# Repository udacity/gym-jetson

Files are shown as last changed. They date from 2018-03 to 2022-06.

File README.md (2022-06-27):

# Archival Note
We are archiving this repository because we do not want learners to push personal development to the current repository. If you have any issues or suggestions to make, feel free to:
- Utilize the https://knowledge.udacity.com/ forum to seek help on content-specific issues.
- Submit a support ticket along with the link to your forked repository if (learners are) blocked for other reasons. Here are the links for the [retail consumers](https://udacity.zendesk.com/hc/en-us/requests/new) and [enterprise learners](https://udacityenterprise.zendesk.com/hc/en-us/requests/new?ticket_form_id=360000279131). 

Udacity - Robotics NanoDegree Program (https://www.udacity.com/robotics)
# Learning Robotics on the Jetson TX2 - Lights Out Robot

Are you ready to learn how to use your Jetson TX2 for robotics applications? In this project, you'll learn how to get started using your TX2 to apply AI to your robotics application. You will get the chance to build a simple “Lights Out” robot that will use reinforcement learning to push buttons and turn out corresponding LEDs. We will cover how to wire up, program, and run the robot. Additionally, we will discuss the basics of applied reinforcement learning.



## Getting Started

1. Start by ordering the parts and gathering the tools listed in the [Bill of Materials](https://github.com/udacity/gym-jetson/blob/master/robot_construction/BOM.md) More information about laser cutting, such as size and thickness of material can also be found there. You will also find the .eps or .dxf file used to laser cut this robot. If you don't have access to a laser cutter, information about ordering the parts using a laser cutting production service is included.

2. Set up your Jetson environment. This project was run on jetPack3.2, and was also tested on 3.1. Python libraries gpio, cffi, smbus, and numpy are required.

```
sudo apt-get install libffi-dev
sudo pip install cffi
sudo pip install smbus-cffi numpy gpio
```

3. Follow the steps for [Assembling the Robot](https://github.com/udacity/gym-jetson/blob/master/robot_construction/assembly.md) 

4. Jupyter notebooks have been created for this project to outline the next steps. The first notebook covers **taking control of the robot**, including assembly and wiring of the electronic components, testing and troubleshooting getting the arm to hit the buttons and have the lights turn on and off. A second notebook discusses **the reinforcement learning component, where we program the robot to play a game**.

To launch the [notebook](https://github.com/udacity/gym-jetson/blob/master/0_Introduction.ipynb) locally from your machine, run the following commands:

``` bash
$ git clone https://github.com/udacity/gym-jetson.git
$ cd gym-jetson
$ jupyter notebook 0_Introduction.ipynb
```

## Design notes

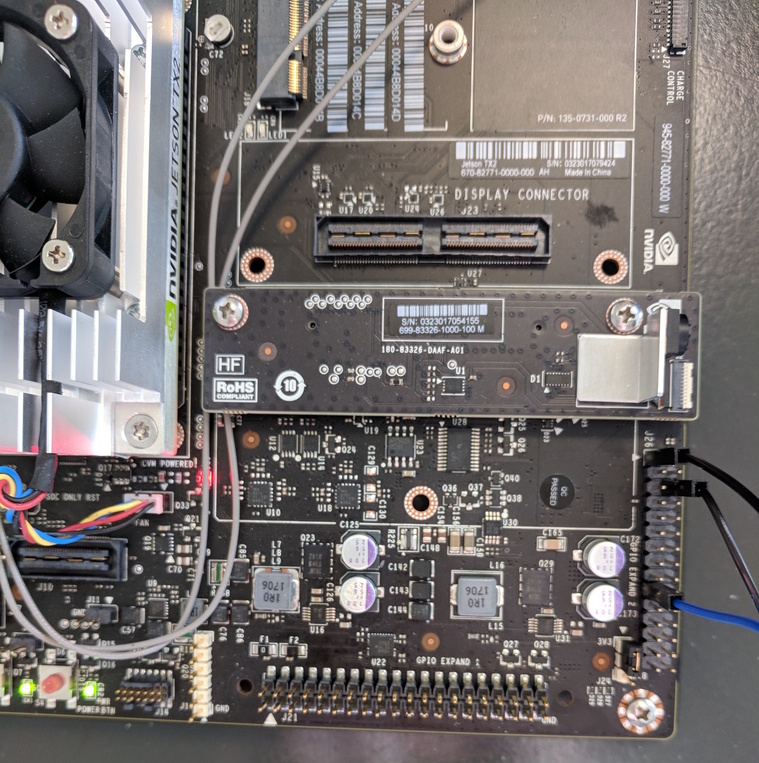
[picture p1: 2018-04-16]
images/jetson4.jpg

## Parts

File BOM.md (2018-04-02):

## Bill of Materials

### Lights Out Robot

| Vendor | Part | Qty.  |
| --- | --- | ----- |
| Sparkfun | [Servo - Hitec HS-422 (Standard Size)](https://www.sparkfun.com/products/11884) | 2 |
| Sparkfun | [Tactile Button Assortment](https://www.sparkfun.com/products/10302) | 1 |
| Sparkfun | [Diffused LED - Blue 10mm](https://www.sparkfun.com/products/10635) | 1 |
| Sparkfun | [Diffused LED - Green 10mm](https://www.sparkfun.com/products/10633) | 1 |
| Sparkfun | [Diffused LED - Yellow 10mm](https://www.sparkfun.com/products/10634) | 1 |
| Sparkfun | [Diffused LED - Red 10mm](https://www.sparkfun.com/products/10632) | 1 |
| Sparkfun | [LED Holder - 10mm (Chrome Finish)](https://www.sparkfun.com/products/11148) | 4 |
| Sparkfun | [SparkFun Pi Servo HAT](https://www.sparkfun.com/products/14328) | 1 |
| Sparkfun | [Resistor 1K Ohm 1/4th Watt PTH - 20 pack](https://www.sparkfun.com/products/13760) | 1 |
| Sparkfun | [Resistor 100 Ohm 1/4th Watt PTH - 20 pack](https://www.sparkfun.com/products/13761) | 1 |
| Sparkfun | [Transistor - NPN (BC337)](https://www.sparkfun.com/products/13689) | 4 |
| Sparkfun | [Machine Screw - Socket Head (6-32 ; 3/8"; 25 pack)](https://www.sparkfun.com/products/12423) | 1 |
| Sparkfun | [Standoff - Aluminum Threaded (6-32; 1-1/4", 4 Pack)](https://www.sparkfun.com/products/13136) | 1 |
| Sparkfun | [Breadboard - Full-Size (Bare)](https://www.sparkfun.com/products/12615) | 1 |
| Sparkfun | [Nut - Metal (4-40, 10 pack)](https://www.sparkfun.com/products/10454) | 1 |
| Sparkfun | [Screw - Phillips Head (1/2", 4-40, 10 pack)](https://www.sparkfun.com/products/10452) | 1 |
| Sparkfun | [Jumper Wires - Connected 6" (M/F, 20 pack)](https://www.sparkfun.com/products/12794) | 1 |
| Sparkfun | [Jumper Wire Kit](https://www.sparkfun.com/products/124) | 1 |
| Sparkfun | [Silicone Bumpers - Large (10x16.5mm, 4 pack)](https://www.sparkfun.com/products/10594) | 1 |
| Fastenal | [Screws for servo horns](https://www.fastenal.com/products/details/75403) | 4 |
| Amazon | [HELLOYEE 2x20 Pins Extra Tall Female 0.1" Pitch Stacking Header for Raspberry Pi A+ Pi Model B+ Pi 2 Pi 3 (Pack of 5)](https://www.amazon.ca/HELLOYEE-Female-Stacking-Header-Raspberry/dp/B071VFG82G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) | 1 |

Laser cut [base and arm](https://github.com/udacity/gym-jetson/blob/master/gtc_base_arm.dxf) on 3mm acrylic

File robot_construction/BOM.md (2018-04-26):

## Bill of Materials

### Lights Out Robot

Laser cut [base and arm dxf](https://github.com/udacity/gym-jetson/blob/master/robot_construction/gtc_base_arm.dxf) or [base and arm eps](https://github.com/udacity/gym-jetson/blob/master/robot_construction/gtc_base_arm.eps)on 3mm acrylic. This design is just under 1 square foot of material (approimately 30.5 cm squared). 

If you do not have access to a laser cutter, you can use a service such as [Ponoko](https://www.ponoko.com/) to have the file cut and sent to you! To do this, you can add a new design > upload your design > navigate to gtc_base_arm.dxf or gtc_base_arm.eps > add material (select plastic) > choose a material (select acrylic, your choice of colour) > choose a thickness (3.0mm) > choose a size (P2 - 384mm). Select "add this material" and "Make it"! 

| Vendor | Part | Qty.  |
| --- | --- | ----- |
| Adafruit | [Standard servo - TowerPro SG-5010 - 5010](https://www.adafruit.com/product/155) | 2 |
| Sparkfun | [Tactile Button Assortment](https://www.sparkfun.com/products/10302) | 1 |
| Sparkfun | [Diffused LED - Blue 10mm](https://www.sparkfun.com/products/10635) | 1 |
| Sparkfun | [Diffused LED - Green 10mm](https://www.sparkfun.com/products/10633) | 1 |
| Sparkfun | [Diffused LED - Yellow 10mm](https://www.sparkfun.com/products/10634) | 1 |
| Sparkfun | [Diffused LED - Red 10mm](https://www.sparkfun.com/products/10632) | 1 |
| Sparkfun | [LED Holder - 10mm (Chrome Finish)](https://www.sparkfun.com/products/11148) | 4 |
| Sparkfun | [SparkFun Pi Servo HAT](https://www.sparkfun.com/products/14328) | 1 |
| Sparkfun | [Resistor 1K Ohm 1/4th Watt PTH - 20 pack](https://www.sparkfun.com/products/13760) | 1 |
| Sparkfun | [Resistor 100 Ohm 1/4th Watt PTH - 20 pack](https://www.sparkfun.com/products/13761) | 1 |
| Sparkfun | [Transistor - NPN (BC337)](https://www.sparkfun.com/products/13689) | 4 |
| Sparkfun | [Machine Screw - Socket Head (6-32 ; 3/8"; 25 pack)](https://www.sparkfun.com/products/12423) | 1 |
| Sparkfun | [Standoff - Aluminum Threaded (6-32; 1-1/4", 4 Pack)](https://www.sparkfun.com/products/13136) | 1 |
| Sparkfun | [Breadboard - Full-Size (Bare)](https://www.sparkfun.com/products/12615) | 1 |
| Sparkfun | [Nut - Metal (4-40, 10 pack)](https://www.sparkfun.com/products/10454) | 1 |
| Sparkfun | [Screw - Phillips Head (1/2", 4-40, 10 pack)](https://www.sparkfun.com/products/10452) | 1 |
| Sparkfun | [Jumper Wires - Connected 6" (M/F, 20 pack)](https://www.sparkfun.com/products/12794) | 1 |
| Sparkfun | [Jumper Wire Kit](https://www.sparkfun.com/products/124) | 1 |
| Sparkfun | [Silicone Bumpers - Large (10x16.5mm, 4 pack)](https://www.sparkfun.com/products/10594) | 1 |
| Fastenal | [Screws for servo horns](https://www.fastenal.com/products/details/75403) | 4 |
| Amazon | [HELLOYEE 2x20 Pins Extra Tall Female 0.1" Pitch Stacking Header for Raspberry Pi A+ Pi Model B+ Pi 2 Pi 3 (Pack of 5)](https://www.amazon.ca/HELLOYEE-Female-Stacking-Header-Raspberry/dp/B071VFG82G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) | 1 |

### Tools Required
| Tool | Notes |
| --- |--- |
| Soldering Iron |  |
| Solder | |
| Wire cutter/ stripper | |
| Glue Gun + Glue | If your robot parts have been cut from acrylic, you could also use acrylic solvent to attach the pieces |
| Flat head screwdriver | |
| Phillips head screwdriver | |
| Socket head driver or allen key | |

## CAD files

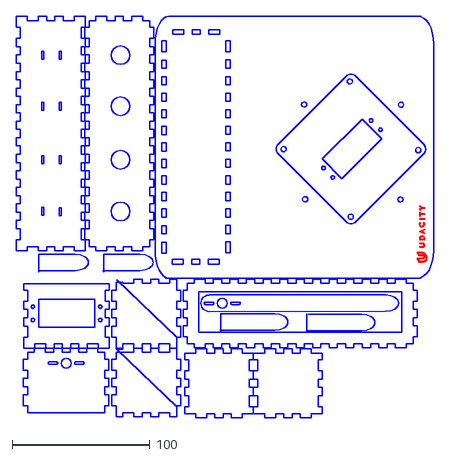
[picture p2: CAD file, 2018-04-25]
robot_construction/gtc_base_arm.dxf
302.8 x 291.3

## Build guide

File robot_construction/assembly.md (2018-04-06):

## Assembly Steps

Before we can use the servo HAT, we need to solder the extra tall 40 pin stacking header onto the servo HAT. Look at the image below to understand how to do this so that it can be plugged into the Jetson and still allow us to plug wires into the exposed pins later on.

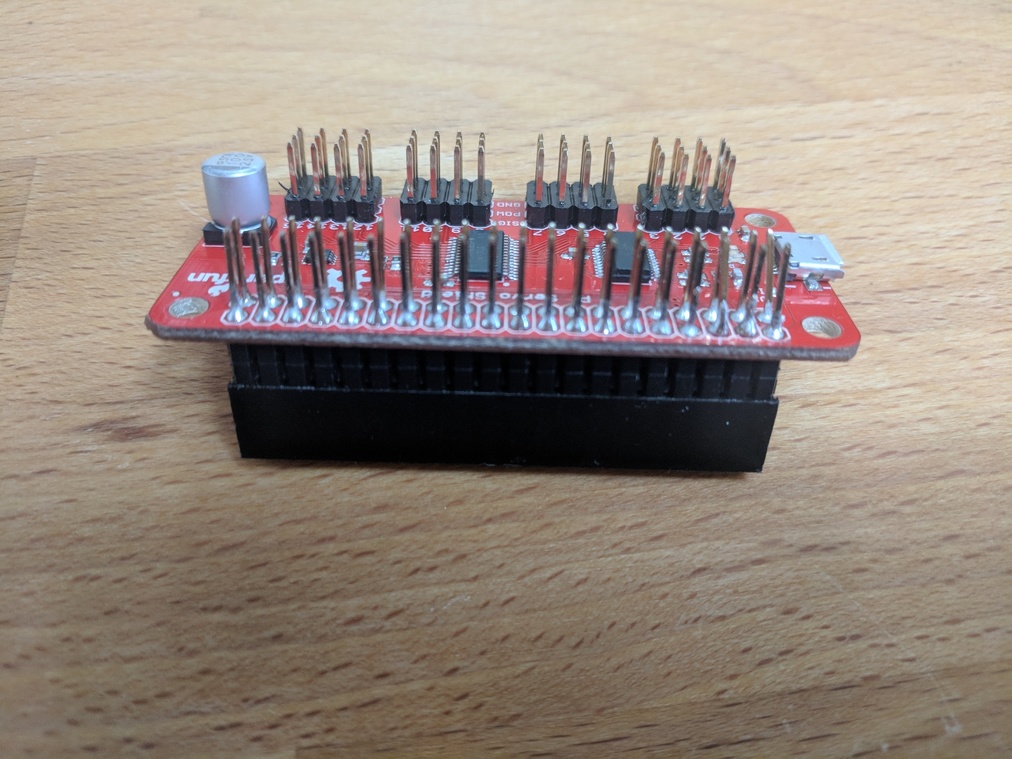
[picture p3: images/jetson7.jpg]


Next,lets use the Jetson and the servo HAT to "zero" both servos to a PWM start time of 0 and an end time of 1250. This will put the servos into a neutral position before we attach the base and arm. This will ensure that the arm is in a starting position from which the positions of the buttons have been calculated to correspond to in later steps.

To do this, plug the servo HAT into the Jetson J21 header as shown below, and plug the pan servo into channel 0 and the tilt servo into channel 1.

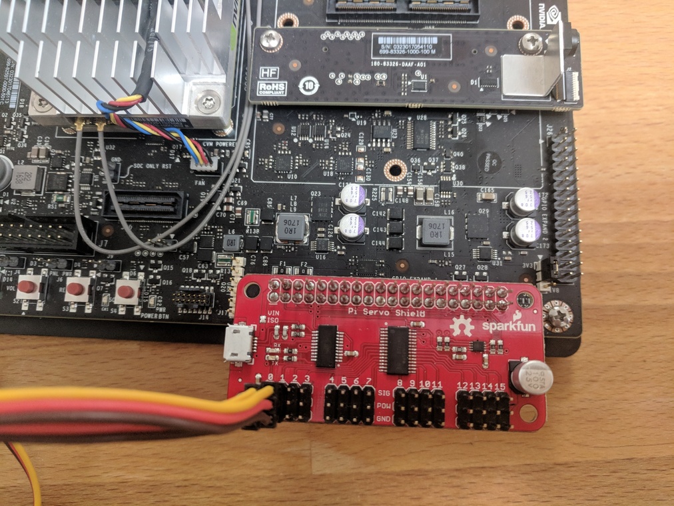
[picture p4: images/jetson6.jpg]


Put the code below into a .py file on the Jetson, and run to initialise the i2c device and write 0 and 1250 as start and stop times to both channel 0 and channel 1 of the HAT. You can find more information about i2c, smbus, and the specific channels that we are writing data to in later steps in the Jupyter notebook.

```
import smbus

#create object of type SMBus, attach it to bus "1"of the Jetson
bus = smbus.SMBus(1)

#the default address of the PWM servo hat is 0x40
addr = 0x40

#enable the PWM chip and tell it to automatically increment addresses after a write to allow for single operation multi-byte writes
bus.write_byte_data(addr, 0, 0x20)
bus.write_byte_data(addr, 0xfe, 0x1e)

#write a start time 0 to the PWM chip for channel 0 and channel 1
bus.write_word_data(addr, 0x06, 0)
bus.write_word_data(addr, 0x0A, 0)

#write an end time to channel 0 and channel 1, which will set the servo motors to their starting position
bus.write_word_data(addr, 0x0C, 1250)
bus.write_word_data(addr, 0x08, 1250)

bus.close()
```

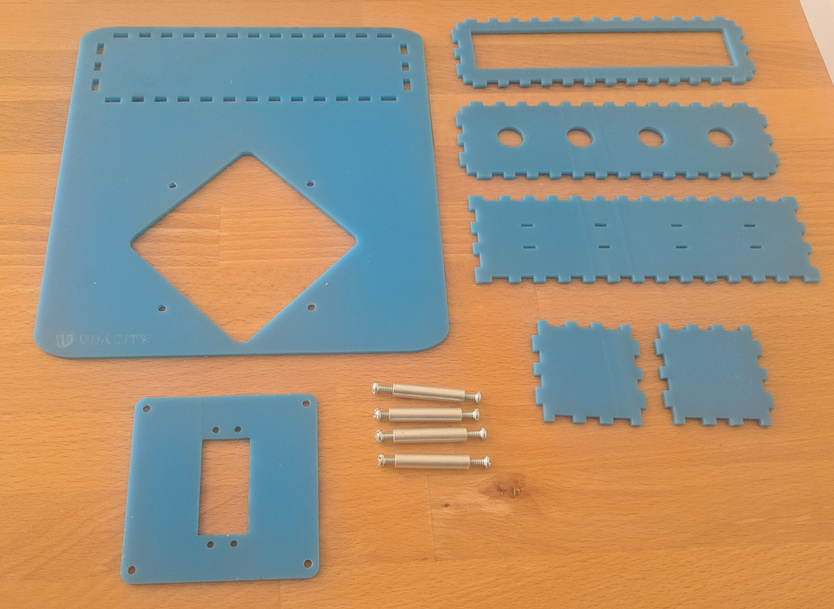
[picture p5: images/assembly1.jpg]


Now we will move on to the assembly of the base!

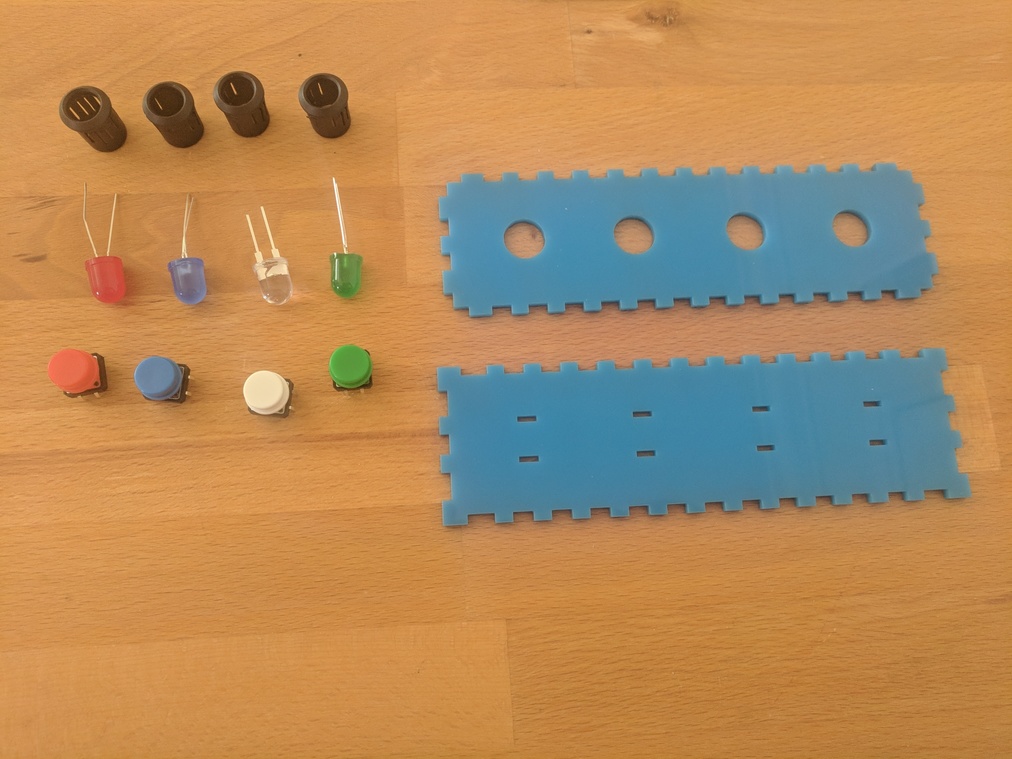
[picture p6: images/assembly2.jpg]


Push an LED into each holder, and attach one to each circular hole on acrylic LED panel assembly.
Set a button in each of the cutouts on the acrylic button panel. Two button leads will sit in each of the rectancular cutouts.
The base of the button will sit flush with the surface of the acrylic button panel. Add a dab of hot glue under each button to attach it to the surface.

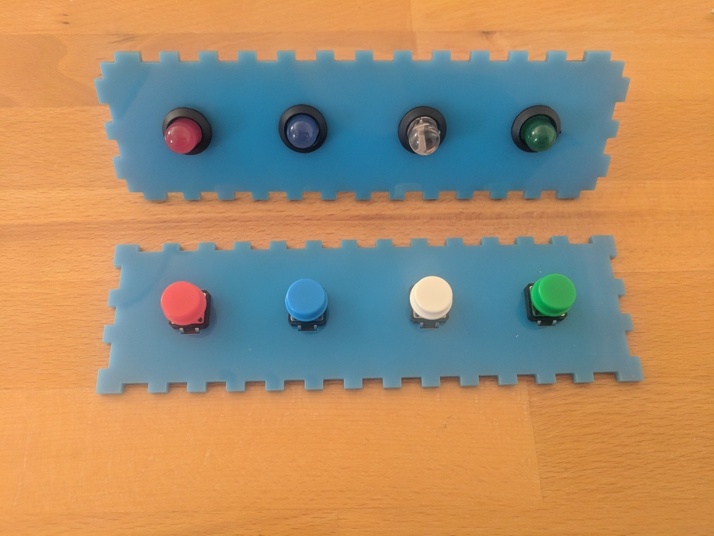
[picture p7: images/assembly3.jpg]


Solder a wire to each LED lead, and add shrink tubing to cover the connection. 
Solder a wire to two of the button leads as shown in the image below.

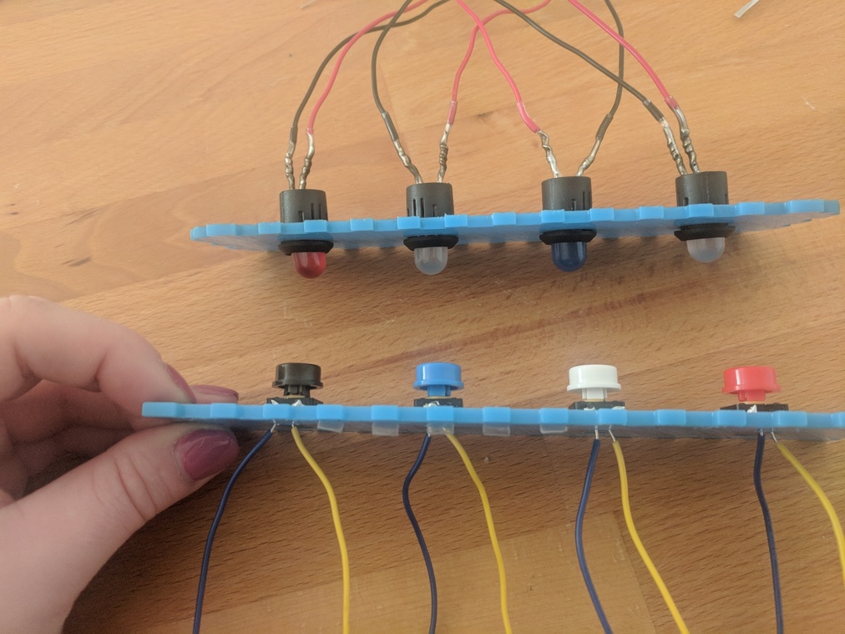
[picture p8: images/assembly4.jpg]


Assemble the button/led panel box, using the side and back pieces. Feed the wires through the rectangular cutout on the back panel. Add some hot glue to the interior edges of the box to adhere.

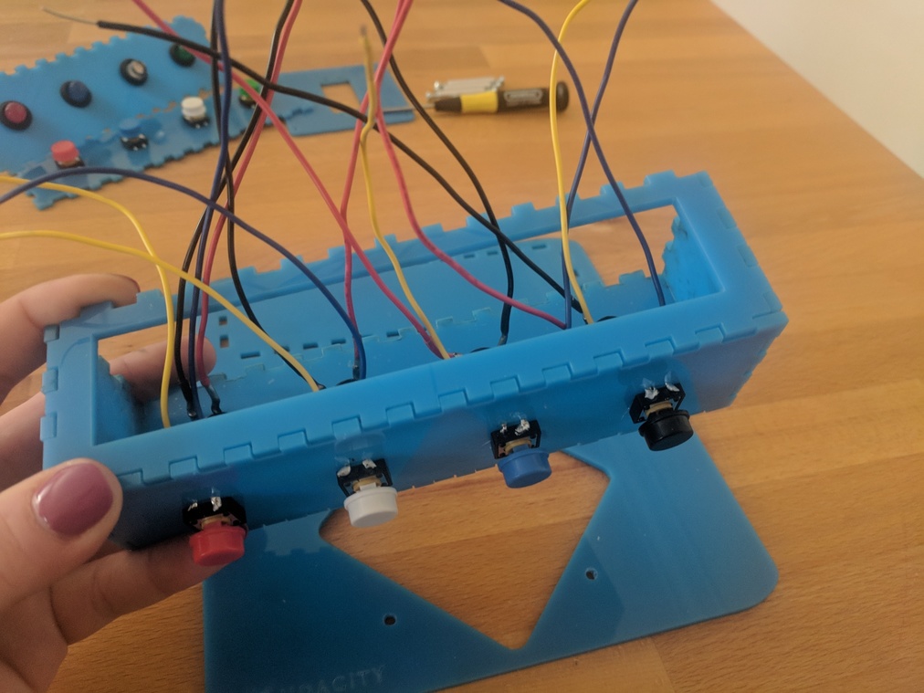
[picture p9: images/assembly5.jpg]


Insert the button/LED panel box into the slots of the robot base plate. Add some hot glue to adhere.

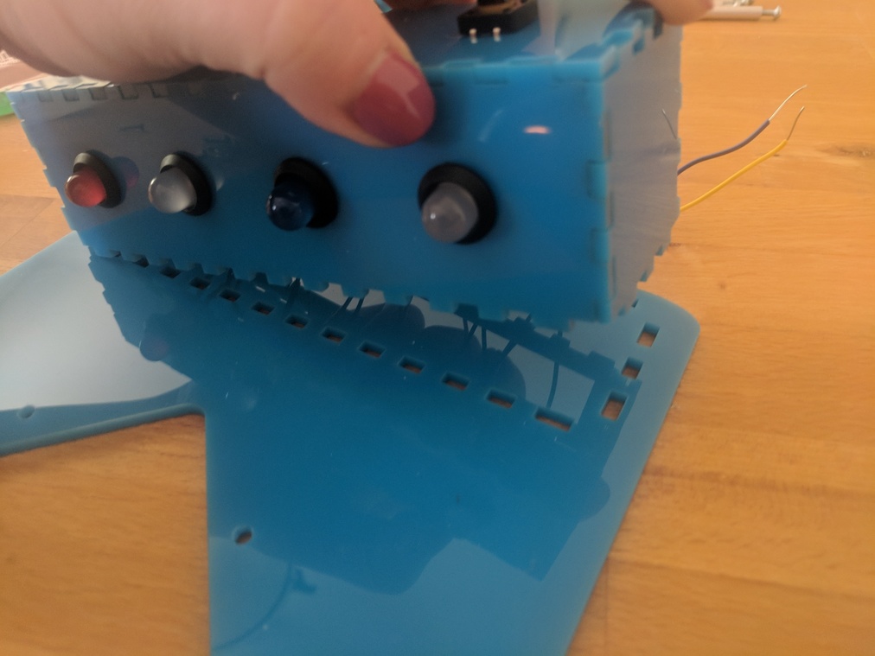
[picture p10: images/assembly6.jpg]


Attach one of the servos to the pan servo base plate as shown in the image below, using 4 screws and 4 nuts.

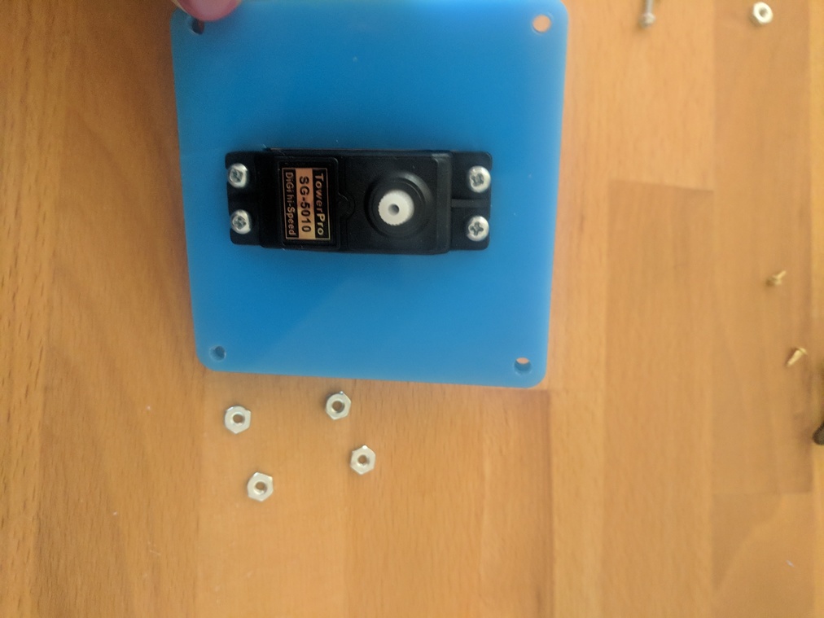
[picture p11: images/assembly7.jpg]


Attach the pan servo base plate to the robot base plate using 4 aluminum standoffs and 8 6-32 screws.

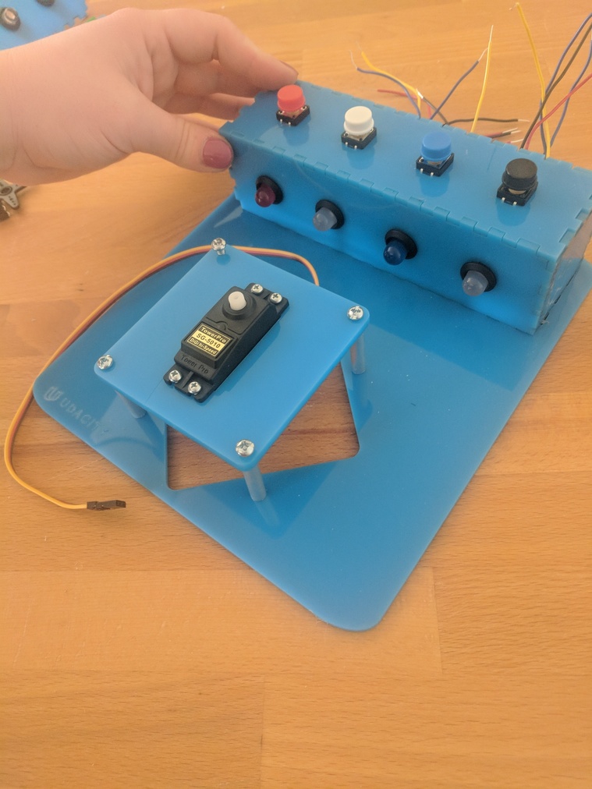
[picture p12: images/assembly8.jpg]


Attach the other servo to the vertical servo plate as shown below using 4 screws and 4 nuts. Also, attach the circular servo horn to the tilt servo base using 2 small gold screws.

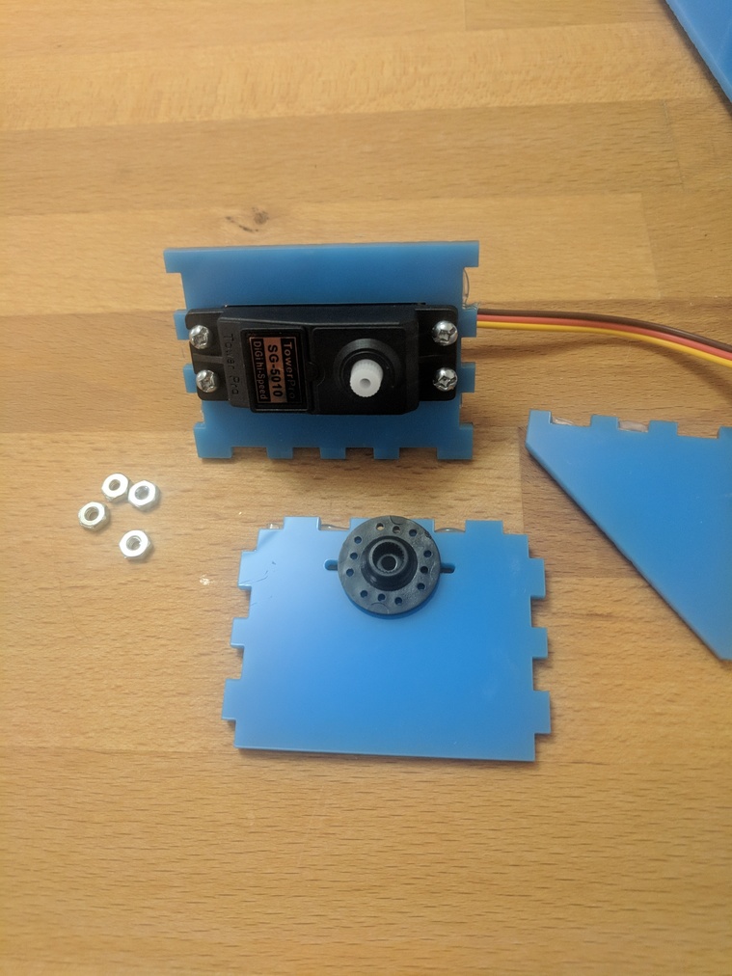
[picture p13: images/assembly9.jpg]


BEFORE the next step, make sure you have used the Jetson and the servo HAT to "zero" the pan servo to a PWM start time of 0 and an end time of 1250 as shown in the first step of this assembly document.

Using the small screw from the servo kit, screw the servo horn/ tilt sevo base to the pan servo as shown below. The orientation of this piece is very important!

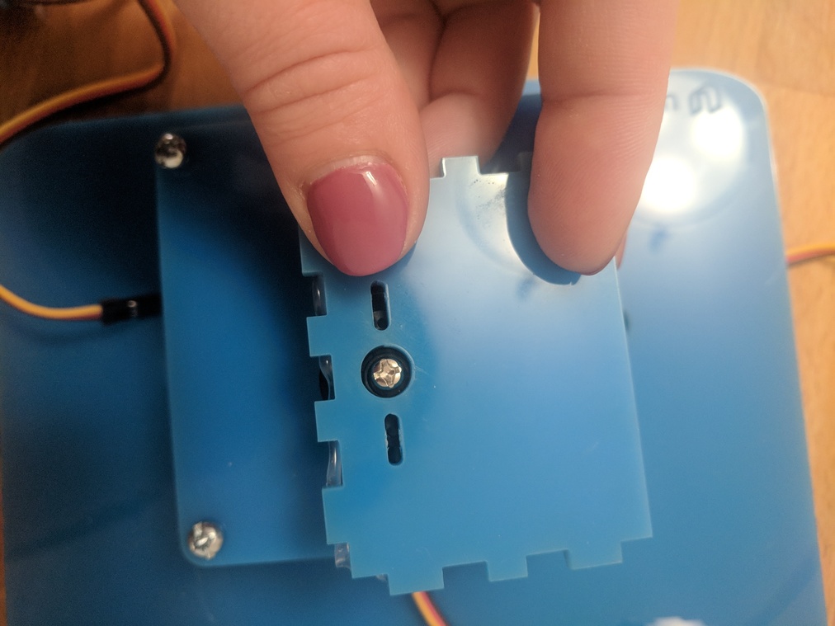
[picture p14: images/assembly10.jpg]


Affix the vertical servo plate and the two triangular support pieces to the tilt servo base in the orientation shown in the image below.

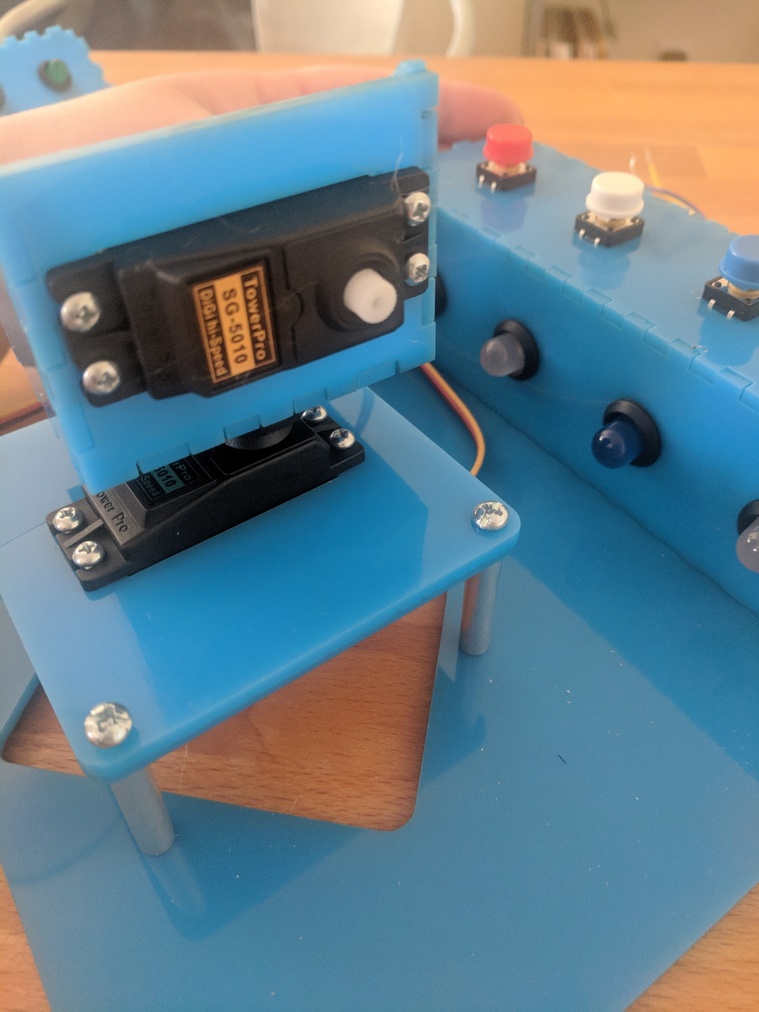
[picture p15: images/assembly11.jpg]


BEFORE the next step, make sure you have used the Jetson and the servo HAT to "zero" the tilt servo to a PWM start time of 0 and an end time of 1250.

Attach the 4-prong servo horn to the robot arm using 2 small gold screws. Using the small screw from the servo kit, screw the servo horn/ robot arm to the tilt servo as shown below. The angle and orientation of this piece is very important.

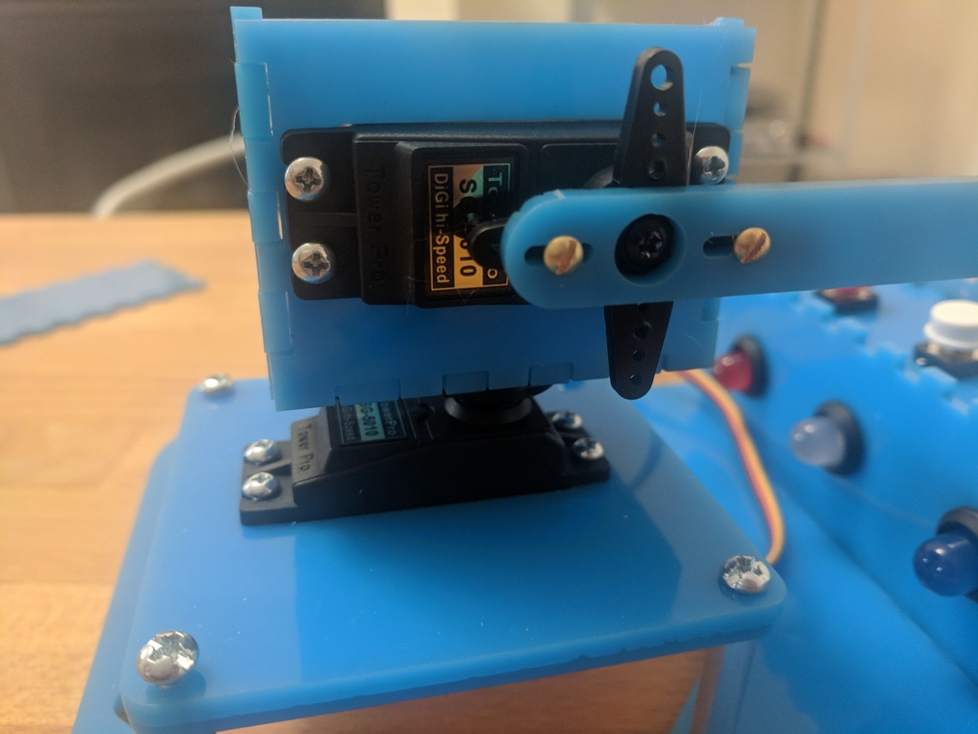
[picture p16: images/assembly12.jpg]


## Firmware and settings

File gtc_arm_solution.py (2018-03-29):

import random
import smbus
import time
import gpio
import sys
import numpy as np
import math
from collections import defaultdict
from jetson_env import JetsonEnv

#assign Jetson sysfs GPIO pins 
in_zero = 300
out_zero = 388

in_one = 398
out_one = 298

in_two = 389
out_two = 299

in_three = 481
out_three = 488

#TODO: change the PWM endtime values below to change the positions the servos move to
#increase the position values to move the arm to the left, and decrease to move to the right. 1 degree = 4.6
position_zero = 1594
position_one = 1457
position_two = 1275
position_three = 1091

arm_neutral = 1250 
#TODO: decrease arm_pressed to move the arm closer to the buttons/ press harder
arm_pressed = 900

#set up the GPIO pins as inputs or outputs, and set outputs to 0
gpio.setup(in_zero, gpio.IN)     # button 0
gpio.setup(out_zero, gpio.OUT)   # led 0
gpio.output(out_zero, 0) #set led 0 to low/off

gpio.setup(in_one, gpio.IN)     # button 1
gpio.setup(out_one, gpio.OUT)   # led 1
gpio.output(out_one, 0) #set led 1 to low/off

gpio.setup(in_two, gpio.IN)    # button 2
gpio.setup(out_two, gpio.OUT)  # led 2
gpio.output(out_two, 0) #set led 2 to low/off

gpio.setup(in_three, gpio.IN)    # button 3
gpio.setup(out_three, gpio.OUT)  # led 3
gpio.output(out_three, 0) #set led 3 to low/off

#create object of type SMBus, attach it to bus "1"of the Jetson
bus = smbus.SMBus(1)

#the default address of the PWM servo hat is 0x40
addr = 0x40
#enable the PWM chip and tell it to automatically increment addresses after a write to allow for single operation multi-byte writes
bus.write_byte_data(addr, 0, 0x20)
bus.write_byte_data(addr, 0xfe, 0x1e)
#write a start time 0 to the PWM chip for channel 0 and channel 1
bus.write_word_data(addr, 0x06, 0)
bus.write_word_data(addr, 0x0A, 0)
#write an end time to channel 0 and channel 1, which will set the servo motors to their starting position
bus.write_word_data(addr, 0x0C, arm_neutral)
bus.write_word_data(addr, 0x08, position_zero)


def led_status():
    """checks each led status, returns which LED currently high"""
    if gpio.read(out_zero) == 1:
        return 0    
    elif gpio.read(out_one) == 1:
        return 1
    elif gpio.read(out_two) == 1:
        return 2
    elif gpio.read(out_three) == 1:
        return 3
    else:
        return 4 # all LEDs are low

def move_to_position(m):
    """change the position of the arm base by writing new end time to PWM chip for channel 0 of servo hat"""
    if m == 0:
        time.sleep(.5)
        bus.write_word_data(addr, 0x08, position_zero)
    elif m == 1:
        time.sleep(.5)
        bus.write_word_data(addr, 0x08, position_one)
    elif m == 2:
        time.sleep(.5)
        bus.write_word_data(addr, 0x08, position_two)
    elif m == 3:
        time.sleep(.5)
        bus.write_word_data(addr, 0x08, position_three)


def push_button(led):
    """change the angle of the arm by writing new end time to PWM chip for channel 1 of servo hat"""
    time.sleep(.5)
    bus.write_word_data(addr, 0x0C, arm_pressed)
    time.sleep(.5)
    bus.write_word_data(addr, 0x0C, arm_neutral)
    button_led_check(led)


def button_led_check(led):
    """checks status of all buttons, and if the correct button has been pressed, LED turns off"""
    button_zero = gpio.read(in_zero)
    button_one = gpio.read(in_one)
    button_two = gpio.read(in_two)
    button_three = gpio.read(in_three)

    if led == 0 and button_zero == 1:
        gpio.output(out_zero, 0)
    elif led == 1 and button_one == 1:
        gpio.output(out_one, 0)
    elif led == 2 and button_two == 1:
        gpio.output(out_two, 0)
    elif led == 3 and button_three == 1:
        gpio.output(out_three, 0)


def dance():
    bus.write_word_data(addr, 0x08, 1594)
    bus.write_word_data(addr, 0x08, 1091)
    bus.write_word_data(addr, 0x08, 1457)
    bus.write_word_data(addr, 0x08, 1275)
    bus.write_word_data(addr, 0x0C, 1600)
    bus.write_word_data(addr, 0x0C, 1400)
    bus.write_word_data(addr, 0x0C, 1600)
    bus.write_word_data(addr, 0x0C, 1250)


def set_arm_position(command, led, arm):
    if command == 0 and arm > 0: # move left
        new_arm = arm-1
        move_to_position(new_arm)
        return (led_status(), new_arm)
    elif command == 1: # stay in current position and push
        push_button(led)
        return (led_status(), arm)
    elif command == 2 and arm < 3: #move right
        new_arm = arm+1
        move_to_position(new_arm)
        return (led_status(), new_arm)
    else:
        return (led_status(), arm)


def light_led(led):
    """led on by setting corresponding gpio pin to 1/ high/ on"""
    if led == 0:
        gpio.output(out_zero, 1)
    elif led == 1:
        gpio.output(out_one, 1)
    elif led == 2:
        gpio.output(out_two, 1)
    elif led == 3:
        gpio.output(out_three, 1)
    else:
        return 0


def reset():
        """Physical switch is momentary, but the sysfs gpio 
        maintains an on state in the software until you toggle it off by resetting the gpio pin"""
        gpio.setup(in_zero,gpio.OUT)
        gpio.setup(in_one, gpio.OUT)
        gpio.setup(in_two, gpio.OUT)
        gpio.setup(in_three, gpio.OUT)

        gpio.setup(in_zero, gpio.IN) # button 1
        gpio.setup(out_zero, gpio.OUT) #led 1
        gpio.output(out_zero, 0)

        gpio.setup(in_one, gpio.IN) #button 2
        gpio.setup(out_one, gpio.OUT) # led 2
        gpio.output(out_one, 0)

        gpio.setup(in_two,gpio.IN) # button 3
        gpio.setup(out_two, gpio.OUT) #led 3
        gpio.output(out_two, 0)

        gpio.setup(in_three,gpio.IN) # button 4
        gpio.setup(out_three, gpio.OUT) # led 4
        gpio.output(out_three, 0)


def get_state(led, arm, nLED=4):
    state = led*nLED + arm
    return state


def play_round(env, Q):
    # reset the game
    reset()
    arm = np.random.choice(env.nLED)
    led = np.random.choice(env.nLED)
    light_led(led)
    move_to_position(arm)

    game_round = []
    state = get_state(led, arm)
    action = np.random.choice(env.nA)
    game_round.append((state, action))

    led, arm = set_arm_position(action, led, arm)
    
    for i in range(14):
        if not led==4:
            state = get_state(led, arm)
            best_actions = np.argwhere(Q[state] == np.amax(Q[state])).flatten() 
            action = random.choice(best_actions)    
            led, arm = set_arm_position(action, led, arm)        
            game_round.append((state, action))    
        else:
            break
            
    return game_round
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

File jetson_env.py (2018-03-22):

import math
import numpy as np

class JetsonEnv():

    def __init__(self, nLED=4, max_move=15):
        self.nLED = nLED                  # number of LEDs
        self.nS = int(math.pow(nLED, 2))  # number of game states
        self.nA = 3                       # number of actions
        self.max_move = max_move          # max number of moves in game

    def reset(self):
        """resets lit LED and arm position to begin game round"""
        self.led = np.random.choice(self.nLED) # initialize lit LED
        self.arm = np.random.choice(self.nLED) # initialize arm position
        self.i_move = 1                        # count moves
        self.done = False                      # True if round ended
        return (self.led, self.arm)

    def get_next_state(self, action):
        """get next game state (as a result of last game move)"""
        self.old_arm = self.arm                          # roll over arm position
        if action==0:                                    # move left 
            self.arm = max(self.old_arm-1, 0)
        elif action==1:                                  # push          
            self.arm = self.old_arm
            if self.led==self.arm:                
                self.done = True
        elif action==2:                                  # move right
            self.arm = min(self.old_arm+1, self.nLED-1)
        if self.i_move >= self.max_move:                 # check if game ended
            self.done = True
        self.i_move += 1                                 # increment move index
            
    def get_points(self, action):
        """get points (as a result of last game move)"""                                            
        points = -1
        return points

    def step(self, action):
        """get next game state and points (as a result of last game move)"""
        self.get_next_state(action)
        points = self.get_points(action)
        return (self.arm, points, self.done)

    def get_random_action(self):
        """select a random action"""
        return np.random.choice(self.nA)

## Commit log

2018-03-08 introduced bug to code, added more description
    [gtc_arm.py, jetson_env.py]
2018-03-23 gtc arm
2018-03-26 variables for arm position, add comments
2018-03-30 Rename Introduction to Reinforcement Learning with NVIDIA Jetson TX2.ipynb to Introduction.ipynb
2018-04-03 Update and rename BOM.md to robot_construction/BOM.md
2018-04-16 modified: assembly1.jpg modified: assembly10.jpg modified: assembly11.jpg modified: assembly12.jpg modified: assembly2.jpg modified: assembly3.jpg modified: assembly4.jpg modified: assembly5.jpg modi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
2018-04-16 modified: jetson1.jpg modified: jetson2.jpg modified: jetson3.jpg modified: jetson4.jpg modified: jetson5.jpg modified: jetson6.jpg modified: jetson7.jpg
2018-04-16 modified: assembly1.jpg modified: assembly10.jpg modified: assembly11.jpg modified: assembly12.jpg modified: assembly2.jpg modified: assembly3.jpg modified: assembly4.jpg modified: assembly5.jpg modi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
2018-04-25 updated files
    [gtc_base_arm.dxf]
